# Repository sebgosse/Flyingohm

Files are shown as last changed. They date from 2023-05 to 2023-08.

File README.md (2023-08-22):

#Flyingohm
__FlyingOhm Remote Source Code__

## 1. Overview of FlyingOhm
FlyingOhm is an electric paramotor project (ULM class 1).

The paramotor consists of : a frame, a motor (with propeller), a battery, a motor controller and a remote control.

Link to facebook page: https://www.facebook.com/FlyingOhm/

Link to the youtube page: https://youtube.com/@SebastienGOSSE

## 2. Presentation of the FlyingOhm project
The project concerns the source code of the remote control which allows (among other things):

-To control the motor via the potentiometer

- To display useful data to the pilot (State of the engine, autonomy, duration of flight, etc.)

## 3. Features
### States and modes
There are 3 states: INIT, DISARMED, ARMED

In the Init state, the FlyingOhm logo is displayed as well as the firmware version.

In Disarmed state, the remote sends a PWM of 1000us (motor OFF)

In the Armed state, the remote control sends the setpoint returned by the potentiometer to the controller

The transition from the Init state to Disarmed is done automatically after a few seconds.

The transition from the Disarmed to Armed state occurs when the pilot has pressed the push button (long press)

The passage from the Armed state to Disaremd takes place when the pilot presses briefly on the push button.

A safety switch is present under the remote control. If this is activated, the remote control is no longer powered and the controller no longer receives a PWM signal => The motor stops.

### PWM signal
The PWM signal is the main element to be sent to the motor controller.

The PWM has a frequency of 50Hz (signal duration of 1000us = 0%, 2000us = 100%)

### Screen display
The screen is divided into different areas as shown in the image below:
<p align="center">
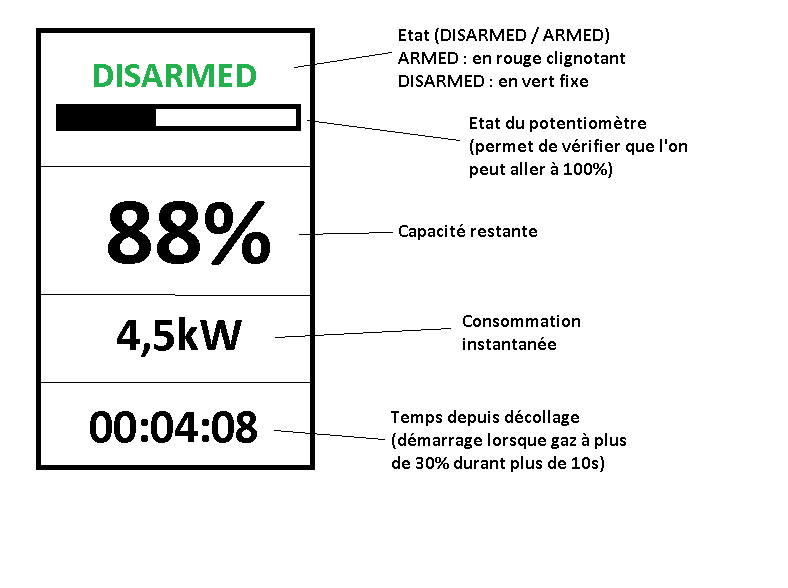
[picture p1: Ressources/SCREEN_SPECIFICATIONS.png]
SCREEN
  
</p>

### Reading controller data
The controller sends a UART signal containing several interesting information to exploit, in particular:

-Total battery voltage

-Controller temperature

-The instantaneous current

Controller documentation reference: https://docs.powerdrives.net/products/hv_pro/uart-telemetry-output

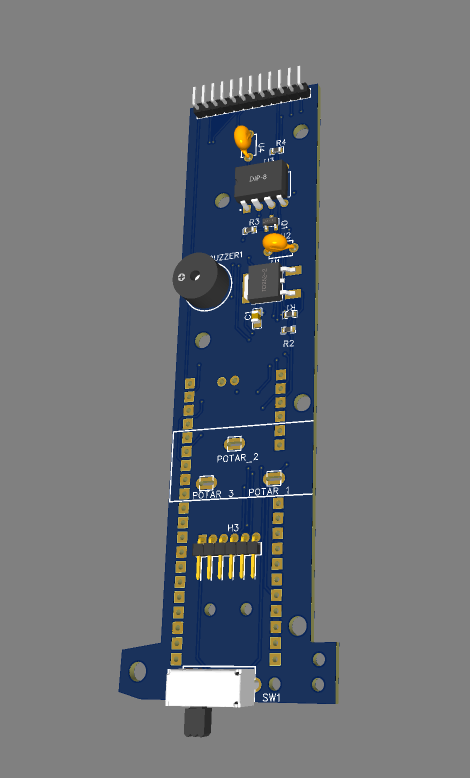
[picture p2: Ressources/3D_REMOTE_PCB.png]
[](Ressources/remote-screen-video.mp4 "Now in Android: 55")

## 4. BOM and Pinout
The project consists of (among others):

-a raspberry pico pi

- an ST7735R screen

-a potentiometer connected to GP27

- a lighted push button connected to GP15 (GP14 for button lighting)

-a buzzer connected to GP12

## 5.PCB
Two PCBs exist: the first for the main handle which contains the pico pi and the potentiometer.
<p align="center">
  3D representation of the main PCB
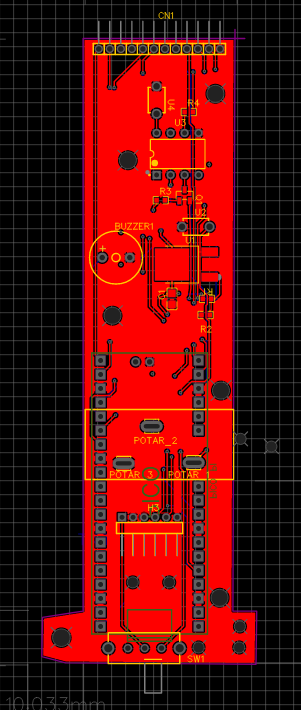
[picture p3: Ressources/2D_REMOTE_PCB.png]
Main PCB routing
  
</p>

The second PCB integrates the screen as well as the push button. This second PCB is soldered vertically on the main PCB.
<p align="center">
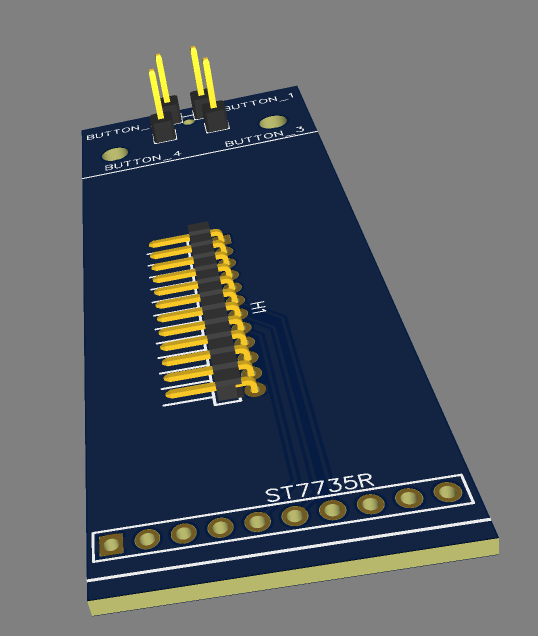
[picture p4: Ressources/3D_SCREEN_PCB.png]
3D representation of the screen PCB
  
</p>

## 6. 3D printing of the remote control
The remote control is then printed in 3D and integrates the PCBs, as well as the electric cable connected to the controller.
<p align="center">
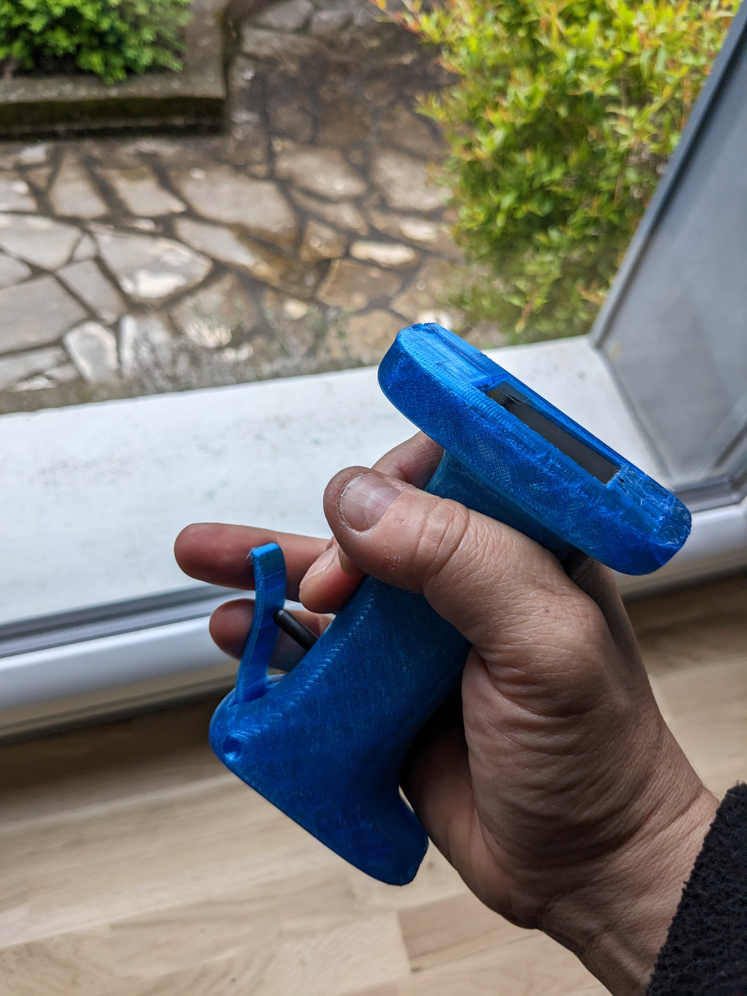
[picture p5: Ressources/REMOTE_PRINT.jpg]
Remote control printing
  
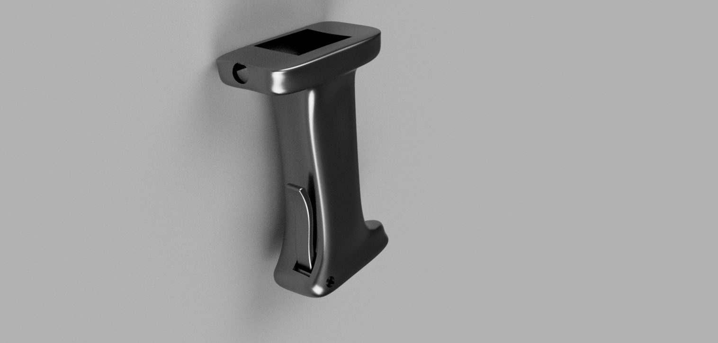
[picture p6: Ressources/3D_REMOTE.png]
3D model of the remote control
  
</p>

## Environment, code and flash of the raspberry pico pi
The IDE used to develop is Thonny.

The interpreter used is circuipython for Rapsberry Pico pi

__Facility__ :

-Connect the Pico Pi via USB to the PC.

-Launch Thonny (when using a pico pi for the first time, you will need to install micropython on the pico pi)

-Copy the libraries/dependencies on the pico pi (librairies, fonts, etc.)

-Open the main.py on Thonny, and execute the scipt (green arrow)

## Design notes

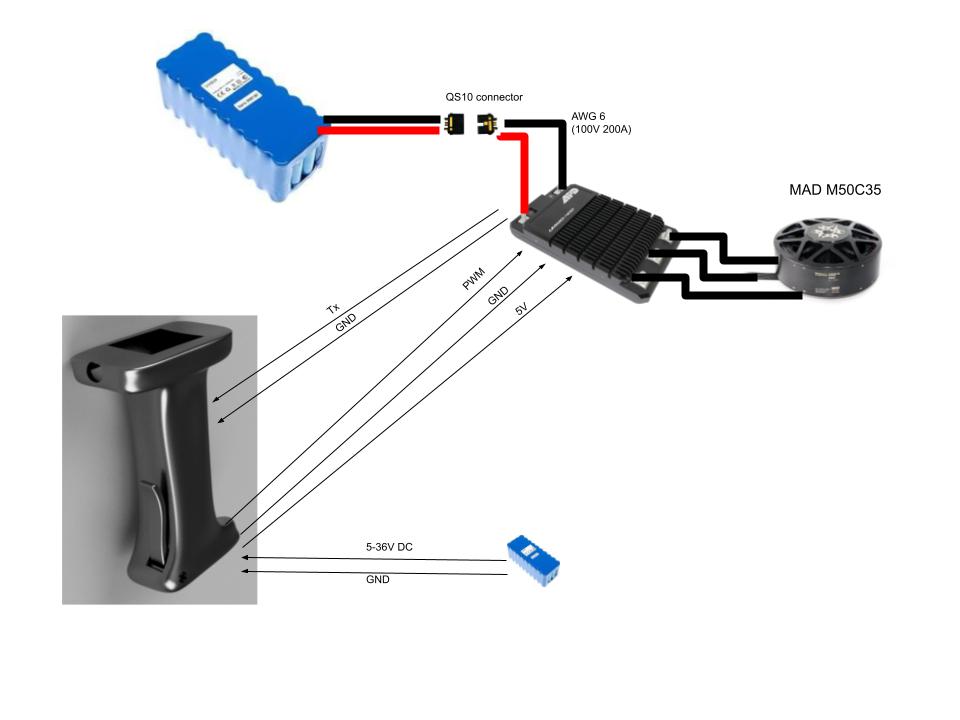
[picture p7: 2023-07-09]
Ressources/Synoptique_remote.jpg

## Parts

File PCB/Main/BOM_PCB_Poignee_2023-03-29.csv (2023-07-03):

ID | Name | Designator | Footprint | Quantity | Manufacturer Part | Manufacturer | Supplier | Supplier Part | Price | Pins | 3DModel | Capacitance | Contributor | Frequency | Package Display | Resistance | Resistance (Ohms) | link
1 | C20526 | Q1 | SOT-23-3_L2.9-W1.3-P1.90-LS2.4-BR | 1 | MMBT3904 | CJ(江苏长电/长晶) | LCSC | C20526 | 0.002 | 3 | SOT-23-3P_L2.9-W1.3-H1.0-LS2.4-P0.95 |  | 立创EDA官方封装库 |  |  |  |  | https://www.diodes.com/assets/Package-Files/SOT23.pdf
2 | A2005WR-12P | CN1 | HDR-TH_12P-P2.00-H-M-W7.0 | 1 | A2005WR-12P | Changjiang Connectors | LCSC | C225279 | 0.04 | 12 | HDR-TH_12P-P2.00-M-WI-1X12P |  | LCSC |  |  |  |  | https://item.szlcsc.com/225561.html
3 | PZ200-1-06-W | H3 | HDR-TH_6P-P2.00-H-M-W7.2-N | 1 | PZ200-1-06-W | HCTL(华灿天禄) | LCSC | C2905972 | 0.007 | 6 | HDR-TH_6P-P2.00-H-M-W7.2-N |  | LCSC |  |  |  |  | https://atta.szlcsc.com/upload/public/pdf/source/20211108/B9097FD167ADAA46D09A37B4E0FC476B.pdf
4 | HNB09A05 | BUZZER1 | BUZ-TH_BD9.6-P5.00-D0.7-FD | 1 | HNB09A05 | 华能 | LCSC | C96493 | 0.036 | 2 | BUZ-TH_D9.0-H5.5-P5.0 |  | 87804271zpf | 3000Hz |  |  |  | https://item.szlcsc.com/200847.html
5 | SK-12E12-G5 | SW1 | SW-TH_SK-12E12-G5 | 1 | SK-12E12-G5 | 韩国韩荣 | LCSC | C136720 | 0.014 | 5 | SW-TH_SK-12E12-G5 |  | LCSC |  |  |  |  | https://item.szlcsc.com/148036.html
6 | 1K | R3,R4 | R0603 | 2 | RC0603FR-071KL | YAGEO(国巨) | LCSC | C22548 |  | 2 | R0603 |  | lcsc |  |  | 1kΩ |  | https://www.mouser.in/datasheet/2/447/PYu_RT_1_to_0_01_RoHS_L_11-1669912.pdf
7 | 6N137_C142297 | U3 | DIP-8_L9.8-W6.6-P2.54-LS7.6-BL | 1 | 6N137 | EVERLIGHT(亿光) | LCSC | C142297 | 0.049 | 8 | DIP-8_L9.8-W6.6-H3.5-LS7.62-P2.54 |  | LCSC |  |  |  |  | https://item.szlcsc.com/47753.html
8 | 63V-0.1μF | U4,U2 | CAP-TH_L4.5-W3.0-P5.00-D1.2 | 2 | CT4-0805-2F4-63V-0.1μF-S | TORCH(火炬) | LCSC | C110254 | 0.006 | 2 | CAP-TH_BD4.5-W3.0-P5.0 | 100nF | LCSC |  |  |  |  | https://item.szlcsc.com/319606.html
9 | 50V-1uF | C1 | C0805 | 1 | 0805B105K500AT | FH(风华) | LCSC | C111768 | 0.003 | 2 | C0805_L2.0-W1.3-H1.3 |  | lcsc |  |  |  |  | https://item.szlcsc.com/373011.html
10 | 240Ω | R1 | R0603 | 1 | 0603WAF2400T5E | UNI-ROYAL(厚声) | LCSC | C23350 |  | 2 | R0603 |  | lcsc |  |  |  | 240 | https://www.mouser.in/datasheet/2/447/PYu_RT_1_to_0_01_RoHS_L_11-1669912.pdf
11 | 715Ω | R2 | R0603 | 1 | RCT03715RFLF | HKR | LCSC | C178047 | 0.001 | 2 | R0603 |  | LCSC |  |  |  | 715 | https://www.mouser.in/datasheet/2/447/PYu_RT_1_to_0_01_RoHS_L_11-1669912.pdf
12 | LM317MDTRKG | U1 | TO-252-2_L6.6-W6.1-P4.57-LS9.9-BR-CW | 1 | LM317MDTRKG | onsemi(安森美) | LCSC | C191896 |  | 3 | TO-252-2L-3P_L6.6-W6.1-H2.3-LS10.1-P4.6 |  | LCSC |  |  |  |  | https://item.szlcsc.com/176608.html
13 | RASPBERRY-PI-PICO | PICO_PI | PICO PI | 1 |  |  |  |  |  | 39 |  |  | kazhida |  | Yes

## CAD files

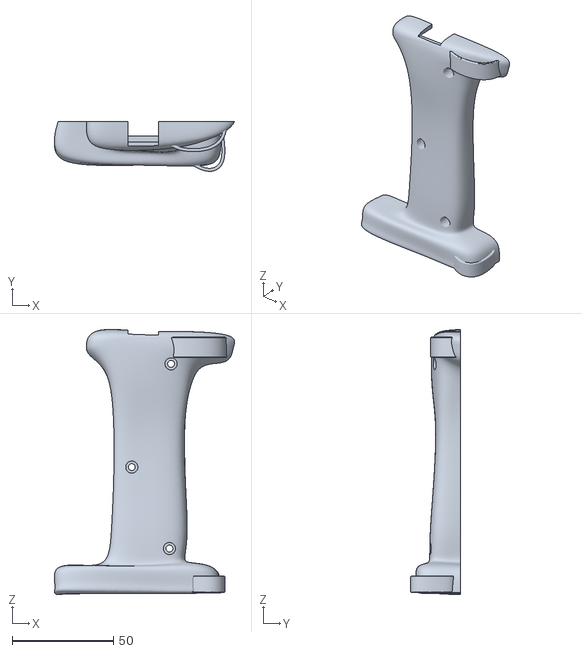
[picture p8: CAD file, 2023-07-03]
3D/Remote_Left_Side.stl
89.1 x 24.6 x 131.0

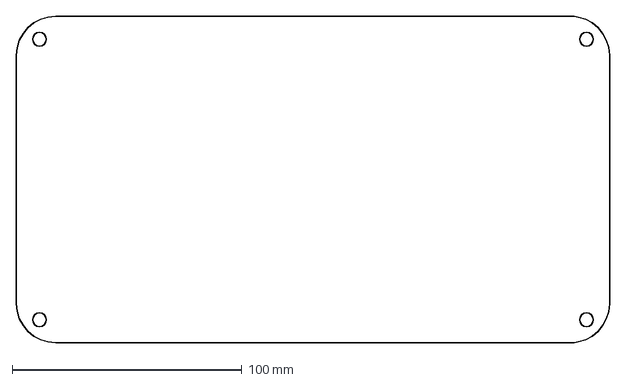
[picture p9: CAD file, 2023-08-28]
Mecanique/dessous_batterie.dxf
258.0 x 142.0 mm

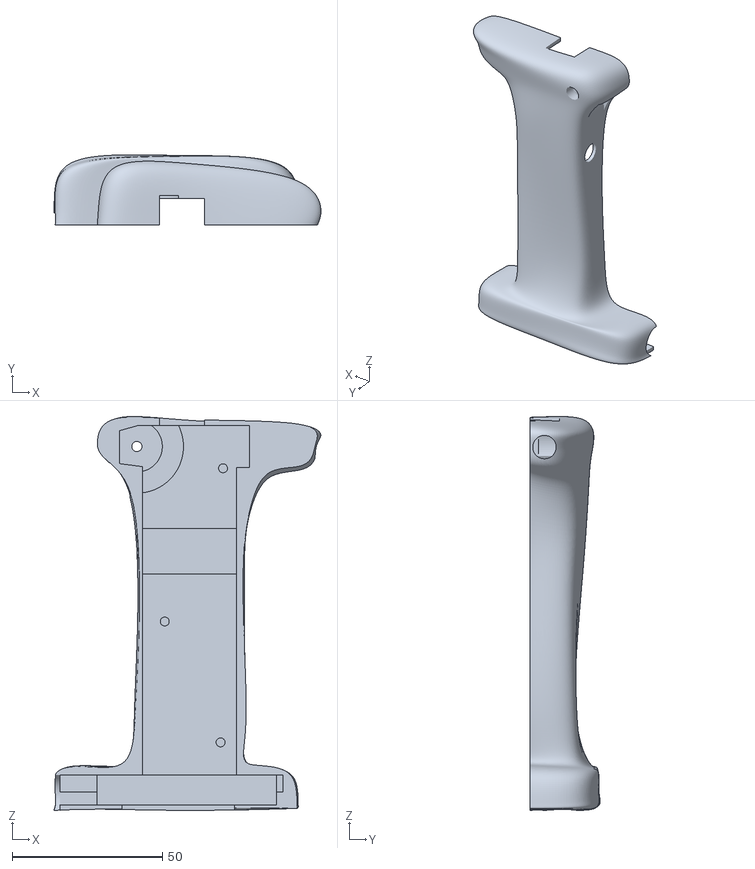
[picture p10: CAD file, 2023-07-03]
3D/Remote_Right_Side.stl
88.9 x 23.4 x 131.3

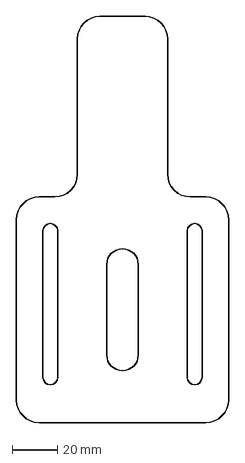
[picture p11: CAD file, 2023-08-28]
Mecanique/Guide_batterie.dxf
94.0 x 180.0 mm

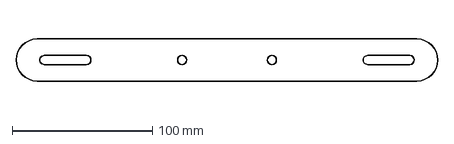
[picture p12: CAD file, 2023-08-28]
Mecanique/Support_selette.dxf
300.7 x 30.0 mm

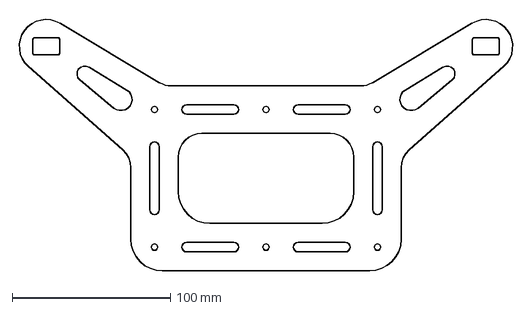
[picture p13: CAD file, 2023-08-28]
Mecanique/Support_esc.dxf
315.8 x 161.1 mm

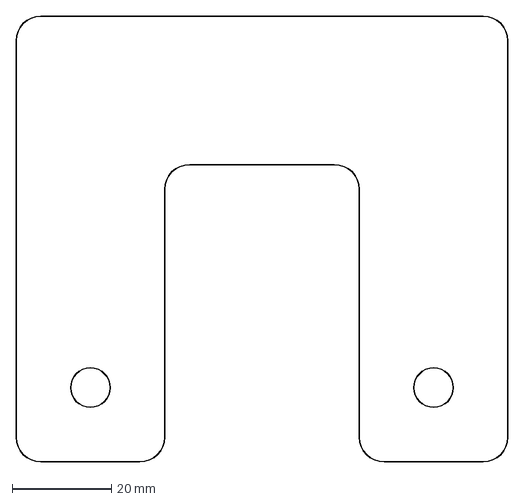
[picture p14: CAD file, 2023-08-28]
Mecanique/Support_sangle_face_avant.dxf
99.3 x 90.0 mm

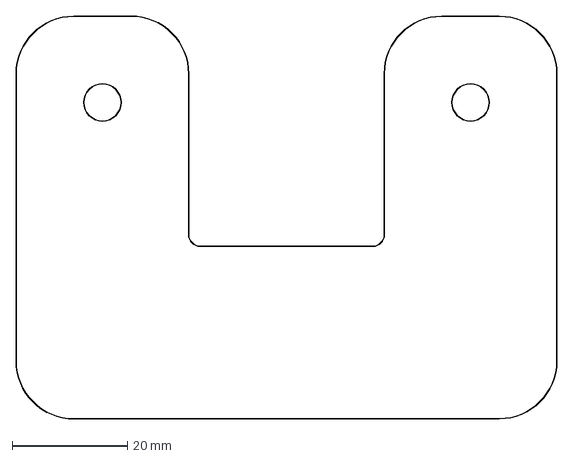
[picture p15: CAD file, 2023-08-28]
Mecanique/Support_sangle_face_arriere.dxf
94.0 x 70.0 mm

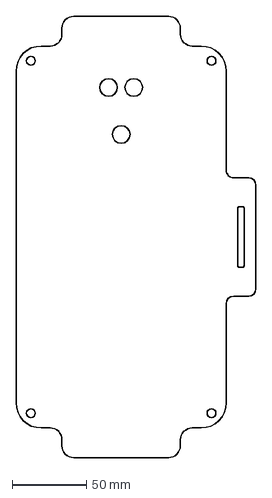
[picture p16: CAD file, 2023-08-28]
Mecanique/Couvercle_batterie.dxf
162.0 x 298.0 mm

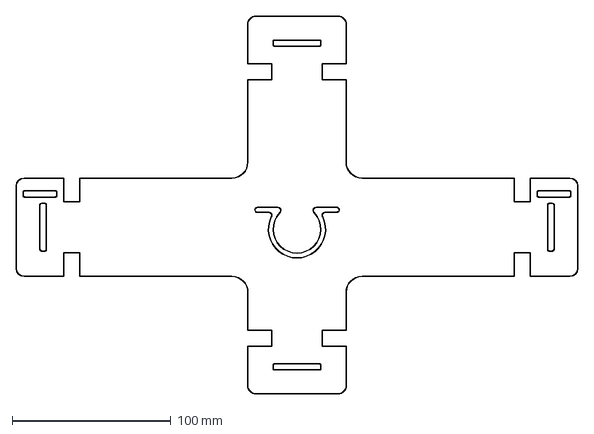
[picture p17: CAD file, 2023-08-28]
Mecanique/Support_batterie.dxf
354.0 x 238.0 mm

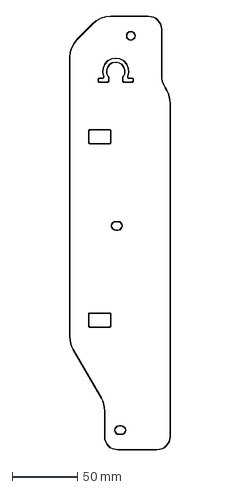
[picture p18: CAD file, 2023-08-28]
Mecanique/Support_principal.dxf
76.5 x 331.0 mm

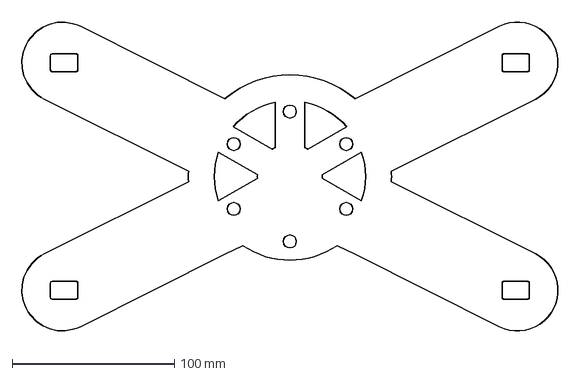
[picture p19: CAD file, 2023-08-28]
Mecanique/Support_moteur.dxf
334.0 x 197.1 mm

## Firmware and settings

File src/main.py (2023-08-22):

import time
import asyncio
import board, busio
import pwmio
from analogio import AnalogIn
import terminalio
from adafruit_simplemath import map_range

import displayio
from adafruit_st7735r import ST7735R
from adafruit_display_text import label
from adafruit_display_shapes.rect import Rect
from adafruit_display_shapes.line import Line

from digitalio import DigitalInOut, Direction, Pull
import vectorio
from adafruit_bitmap_font import bitmap_font

MODE_FONT = bitmap_font.load_font("fonts/ic8x8u.bdf")

#PWM Signal is between 1000us (0%) and 2000us (100%) 
pwm_low_us = 1000 # signal duration of pwm for 0% power
pwm_high_us = 2000 # signal duration of pwm for 100% power
pwm_frequency = 50 # Frequency of PWM signal sent
pwm_low_ratio = (pwm_low_us/((1/pwm_frequency)*1000000)) #Percentage for 0% power motor
pwm_high_ratio = (pwm_high_us/((1/pwm_frequency)*1000000)) #Percentage for 100% power motor
pwm_low = pwm_low_ratio * 65535
pwm_high = pwm_high_ratio * 65535


class Timer:
    def __init__(self):
        self.seconds=0
        self.start_seconds=0
        
    async def start_timer(self):
        while True :
            if (sm.state == "ARMED"):
                flying_time_s = int(time.monotonic()) - self.start_seconds
                screen.timer_text.text = str(flying_time_s//3600) + ":" + str('{:02d}'.format((flying_time_s//60)%60)) + ":" + str('{:02d}'.format(flying_time_s%60))
            await asyncio.sleep_ms(100)      
            pass
    
    def reset_timer(self):
        self.start_seconds=int(time.monotonic())
        
class Button:
    def __init__(self):
        self.pin = DigitalInOut(board.GP15)
        self.pin.direction = Direction.INPUT
        self.pin.pull = Pull.UP

    # Short pressed button detection (armed to disarmed state)
    async def short_pressed_disarm(self): 
        # Wait for button release
        while self.pin.value == 0:
            await asyncio.sleep_ms(100)
            pass
   
        # Wait for button press
        while self.pin.value == 1:
            await asyncio.sleep_ms(100)        
            pass    
   
        sm.transition("ARMED_TO_DISARMED") 
        return True

    # Long pressed button detection (disarmed to armed state)
    async def long_pressed_arm(self):

        nb_cycles = 30 # Number of 100ms cycle needed to switch to armed mode
        while True :
            # Wait for button release
            while (self.pin.value):
                await asyncio.sleep_ms(100)
            y = 0
            while (not self.pin.value):
                screen.rect_arming.width = int(128 * (y/nb_cycles))
                y = y+1
                if (y>nb_cycles):
                    break
                await asyncio.sleep_ms(100)      
                pass
            
            if (y>nb_cycles):
                screen.rect_arming.width = 0                                 
                sm.transition("DISARMED_TO_ARMED")
                return True
            else:
                screen.rect_arming.width = 0                 

class Buzzer:
    def __init__(self):
        pass
#         self.pwm = PWM(Pin(12))
#         self.buzzer_off_delay = 2000 #Durée du bip lorsque le moteur est armé (en ms)
#         self.buzzer_on_delay = 100 #Durée du silence lorsque le moteur est armé (en ms)

    def playtone(self,frequency):
        self.pwm.duty_u16(5000)
        self.pwm.freq(frequency)

    def bequiet(self):
        self.pwm.duty_u16(0)

    async def playsong(self):
        tone_state = 1
        while True :
            try:            
                if (tone_state == 0):
                    self.bequiet()
                    tone_state = 1

                    await asyncio.sleep_ms(self.buzzer_off_delay)                
                else:
                    self.playtone(500)
                    tone_state = 0
                    await asyncio.sleep_ms(self.buzzer_on_delay)
            except asyncio.core.CancelledError:  
                 self.bequiet()
                 return
        self.bequiet()

class Esc:
    def __init__(self):
        self.uart = busio.UART(rx=board.GP13, baudrate=115200)        
        self.pwm = pwmio.PWMOut(board.GP0, frequency=pwm_frequency, duty_cycle=0)
        #Set 0% Power
        self.pwm.duty_cycle = int(pwm_low)
        print(str(pwm_low))
            
    async def send_PWM(self):
        while True:
            #data = self.uart.read(1)  # read up to 32 bytes
            #if data is not None:
                # convert bytearray to string
                #data_string = ''.join([chr(b) for b in data])
                #print(data_string, end="")                
            val = potentiometer.value
            power = int(map_range(val, 0, 65535, pwm_low , pwm_high))
            #Set Power regarding potentiometer           
            self.pwm.duty_cycle = int(power)     
            await asyncio.sleep_ms(20)
            pass
        
    def send_PWM_0(self):
        self.pwm.duty_cycle = int(pwm_low)


class Display:
    def __init__(self):
        mosi_pin = board.GP11
        clk_pin = board.GP10
        reset_pin = board.GP17
        cs_pin = board.GP18
        dc_pin = board.GP16

        displayio.release_displays()
        spi = busio.SPI(clock=clk_pin, MOSI=mosi_pin)
        display_bus = displayio.FourWire(spi, command=dc_pin, chip_select=cs_pin, reset=reset_pin)
        self.display = ST7735R(display_bus, width=128, height=160, bgr = True, auto_refresh=True)
        splash = displayio.Group()
        self.display.show(splash)
        
        ###########
        ## FIRST GROUP : MODE AND POWER BAR
        ###########
        
        #Draw power bar and arming bar
        palette = displayio.Palette(1)
        palette_vert = displayio.Palette(1)
        palette[0] = 0xFF0000
        palette_vert[0] = 0x00FF00        
        self.rect_power = vectorio.Rectangle(pixel_shader=palette, width=1, height=5, x=0, y=14)
        self.rect_arming = vectorio.Rectangle(pixel_shader=palette_vert, width=1, height=5, x=0, y=8)        
        # Draw Mode (Armed/Disarmed)
        text_mode = "INIT"        
        first_group = displayio.Group(scale=1, x=11, y=24)        
        self.text_area = label.Label(MODE_FONT, text=text_mode, color=0xFFFFFF, scale=2)
        first_group.append(self.text_area)  # Subgroup for text scaling
        first_group.append(self.rect_arming)        
        first_group.append(self.rect_power)
        first_group.append(Line(0, 20, 128, 20, 0xFFFFFF))
        self.rect_arming.width = 0            
        
        ###########
        ## SECOND GROUP : AUTONOMY
        ###########
        
        autonomy = "100%"        
        second_group = displayio.Group(scale=1, x=11, y=70)        
        self.text_autonomy = label.Label(MODE_FONT, x=10, text=autonomy, color=0xFFFFFF, scale=3)
        second_group.append(self.text_autonomy)  # Subgroup for text scaling
        second_group.append(Line(0, 20, 128, 20, 0xFFFFFF))        
        
        ###########
        ## THIRD GROUP : CONSUMPTION
        ###########

        consumption = "0W"        
        third_group = displayio.Group(scale=1, x=11, y=100)        
        self.text_consumption = label.Label(MODE_FONT, x=40, y=5 , text=consumption, color=0xFFFFFF, scale=2)
        third_group.append(self.text_consumption)  # Subgroup for text scaling
        third_group.append(Line(0, 20, 128, 20, 0xFFFFFF))   

        ###########
        ## FOURTH GROUP : TIMER
        ###########
        
        # Draw timer
        fourth_group = displayio.Group(scale=1, x=11, y=130)
        text_timer = "0:00:00"
        self.timer_text = label.Label(MODE_FONT, text=text_timer, color=0xFFFFFF, scale=2)
        self.timer_text.y = 15
        fourth_group.append(self.timer_text)  # Subgroup for text scaling        


        splash.append(first_group)
        splash.append(second_group)
        splash.append(third_group)        
        splash.append(fourth_group)        


class Potentiometer:
    def __init__(self):
        self.adc = AnalogIn(board.A1)
        self.value = 0

    # Potentiometer reading  
    async def read(self):
        while True:
            self.value = self.adc.value
            # Update Power Bar on screen
            screen.rect_power.width = int((self.value / 65536) * 128)
            await asyncio.sleep_ms(20)
            pass        

class StateMachine:
    def __init__(self):
        self.state = "INIT"
        asyncio.create_task(potentiometer.read())
        self.start_timer_task = asyncio.create_task(timer.start_timer())
        print("INIT State")
        
    def transition(self, event):
        if self.state == "INIT" and event == "INIT_TO_DISARMED":
            self.state = "DISARMED"
            print("_INIT_TO_DISARM")
            self.display_state()
            asyncio.create_task(button.long_pressed_arm())            
            print("Transition from INIT to DISARMED")
        elif self.state == "DISARMED" and event == "DISARMED_TO_ARMED":
            self.state = "ARMED"
            self.display_state()
            timer.reset_timer()              
            asyncio.create_task(button.short_pressed_disarm())
            self.send_pwm_task = asyncio.create_task(esc.send_PWM())               
            print("Transition from DISARMED to ARMED")
        elif self.state == "ARMED" and event == "ARMED_TO_DISARMED":
            self.state = "DISARMED"
            self.send_pwm_task.cancel()
            esc.send_PWM_0()
            self.display_state()
            asyncio.create_task(button.long_pressed_arm())               
            print("Transition from ARMED to DISARMED")
        else:
            print("Invalid transition")

            
    def display_state(self):
        if (self.state == "ARMED"):
            screen.text_area.x = 20
            screen.text_area.color = 0xFF0000
            screen.text_area.text = "ACTIF"
        elif (self.state == "DISARMED"):
            screen.text_area.x = 0            
            screen.text_area.color = 0x00FF00
            screen.text_area.text= "INACTIF"
        else:
            screen.text_area.x = 0            
            screen.text_area.color = 0xFFFFFF
            screen.text_area.text= "UNKNOWN"

    async def run(self):
        while True:
            if self.state == "INIT":
                #screen.draw_bmp()
                print("INIT")
                self.transition("INIT_TO_DISARMED")
                print("INIT TO DISARM")                
            await asyncio.sleep_ms(100)
                 

#if __name__ == "__main__":

timer = Timer()
esc = Esc()
potentiometer = Potentiometer()
screen = Display()
button = Button()
buzzer = Buzzer()
sm = StateMachine()
asyncio.run(sm.run())

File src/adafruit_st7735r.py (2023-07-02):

# SPDX-FileCopyrightText: 2019 Scott Shawcroft for Adafruit Industries
# SPDX-FileCopyrightText: 2019 Melissa LeBlanc-Williams for Adafruit Industries
#
# SPDX-License-Identifier: MIT

"""
`adafruit_st7735r`
====================================================

Displayio driver for ST7735R based displays.

* Author(s): Scott Shawcroft and Melissa LeBlanc-Williams

Implementation Notes
--------------------

**Hardware:**

* `1.8" SPI TFT display, 160x128 18-bit color
  <https://www.adafruit.com/product/618>`_ (Product ID: 618)
* `Adafruit 0.96" 160x80 Color TFT Display w/ MicroSD Card Breakout
  <https://www.adafruit.com/product/3533>`_ (Product ID: 3533)
* `1.8" Color TFT LCD display with MicroSD Card Breakout:
  <https://www.adafruit.com/product/358>`_ (Product ID: 358)
* `Adafruit 1.44" Color TFT LCD Display with MicroSD Card breakout:
  <https://www.adafruit.com/product/2088>`_ (Product ID: 2088)
* `Adafruit Mini Color TFT with Joystick FeatherWing:
  <https://www.adafruit.com/product/3321>`_ (Product ID: 3321)

**Software and Dependencies:**

* Adafruit CircuitPython firmware for the supported boards:
  https://circuitpython.org/downloads

"""
try:
    # used for typing only
    from typing import Any
except ImportError:
    pass

import displayio

__version__ = "1.5.12"
__repo__ = "https://github.com/adafruit/Adafruit_CircuitPython_ST7735R.git"

_INIT_SEQUENCE = bytearray(
    b"\x01\x80\x96"  # SWRESET and Delay 150ms
    b"\x11\x80\xff"  # SLPOUT and Delay
    b"\xb1\x03\x01\x2C\x2D"  # _FRMCTR1
    b"\xb2\x03\x01\x2C\x2D"  # _FRMCTR2
    b"\xb3\x06\x01\x2C\x2D\x01\x2C\x2D"  # _FRMCTR3
    b"\xb4\x01\x07"  # _INVCTR line inversion
    b"\xc0\x03\xa2\x02\x84"  # _PWCTR1 GVDD = 4.7V, 1.0uA
    b"\xc1\x01\xc5"  # _PWCTR2 VGH=14.7V, VGL=-7.35V
    b"\xc2\x02\x0a\x00"  # _PWCTR3 Opamp current small, Boost frequency
    b"\xc3\x02\x8a\x2a"
    b"\xc4\x02\x8a\xee"
    b"\xc5\x01\x0e"  # _VMCTR1 VCOMH = 4V, VOML = -1.1V
    b"\x20\x00"  # _INVOFF
    b"\x36\x01\x18"  # _MADCTL bottom to top refresh
    # 1 clk cycle nonoverlap, 2 cycle gate rise, 3 sycle osc equalie,
    # fix on VTL
    b"\x3a\x01\x05"  # COLMOD - 16bit color
    b"\xe0\x10\x02\x1c\x07\x12\x37\x32\x29\x2d\x29\x25\x2B\x39\x00\x01\x03\x10"  # _GMCTRP1 Gamma
    b"\xe1\x10\x03\x1d\x07\x06\x2E\x2C\x29\x2D\x2E\x2E\x37\x3F\x00\x00\x02\x10"  # _GMCTRN1
    b"\x13\x80\x0a"  # _NORON
    b"\x29\x80\x64"  # _DISPON
)


# pylint: disable=too-few-public-methods
class ST7735R(displayio.Display):
    """
    ST7735R display driver

    :param displayio.FourWire bus: bus that the display is connected to
    :param bool bgr: (Optional) An extra init sequence to append (default=False)
    :param bool invert: (Optional) Invert the colors (default=False)
    """

    def __init__(
        self,
        bus: displayio.FourWire,
        *,
        bgr: bool = False,
        invert: bool = False,
        **kwargs: Any
    ):
        init_sequence = _INIT_SEQUENCE
        if bgr:
            init_sequence += (
                b"\x36\x01\xC0"  # _MADCTL Default rotation plus BGR encoding
            )
        else:
            init_sequence += (
                b"\x36\x01\xC8"  # _MADCTL Default rotation plus RGB encoding
            )
        if invert:
            init_sequence += b"\x21\x00"  # _INVON
        super().__init__(bus, init_sequence, **kwargs)

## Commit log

2023-06-01 modification max pwm a 2000
2023-06-05 Ajout de la sonnerie du buzzer lorsque l'on arme le moteur
    [main.py]
2023-07-02 Switching to circuipython
2023-07-09 Update PWM pin and pwm value when armed
